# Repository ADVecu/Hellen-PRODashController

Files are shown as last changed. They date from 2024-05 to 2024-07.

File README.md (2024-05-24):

# FAQ

Q: How do I get latest hellen-one?

A: ``.github/workflows/update-hellen-one-reference.yaml`` is set to pull latest hellen daily!

Q: I get "Cannot parse position" with negative value?

A: Please move origin point into left-bottom corner of the board since we cannot parse negative coordinates at the moment. See https://github.com/andreika-git/hellen-one/issues/349

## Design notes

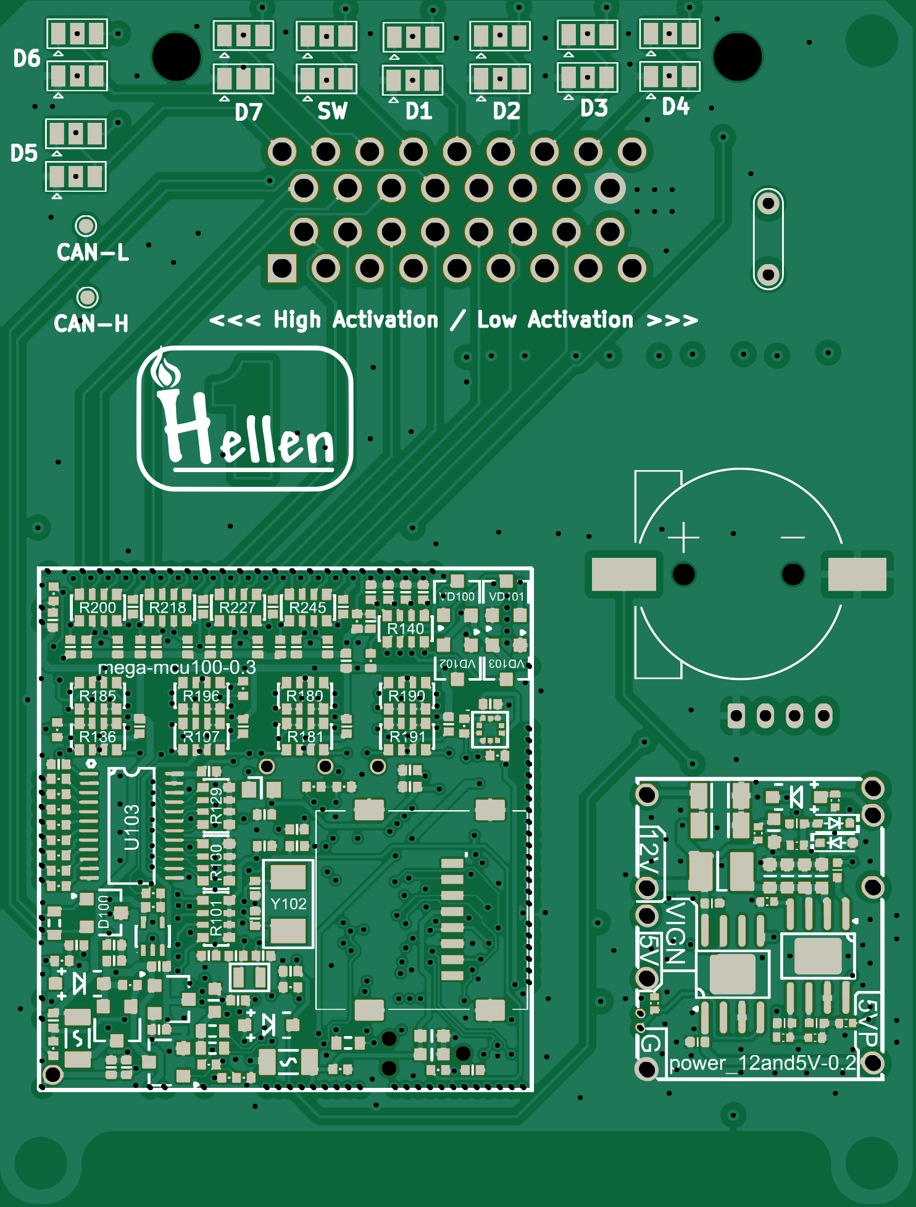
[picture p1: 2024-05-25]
boards/PRODashController-A/board/misc/PRODashController-A-bottom.png

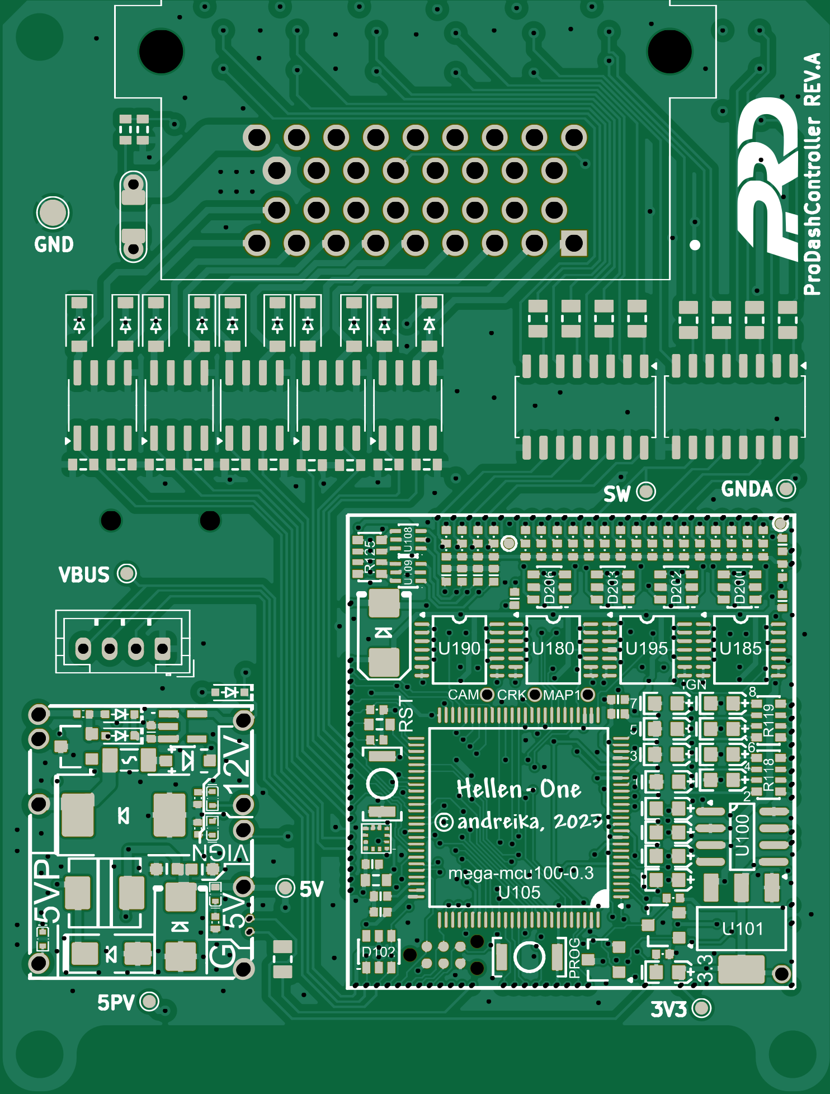
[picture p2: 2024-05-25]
boards/PRODashController-A/board/misc/PRODashController-A-top.png

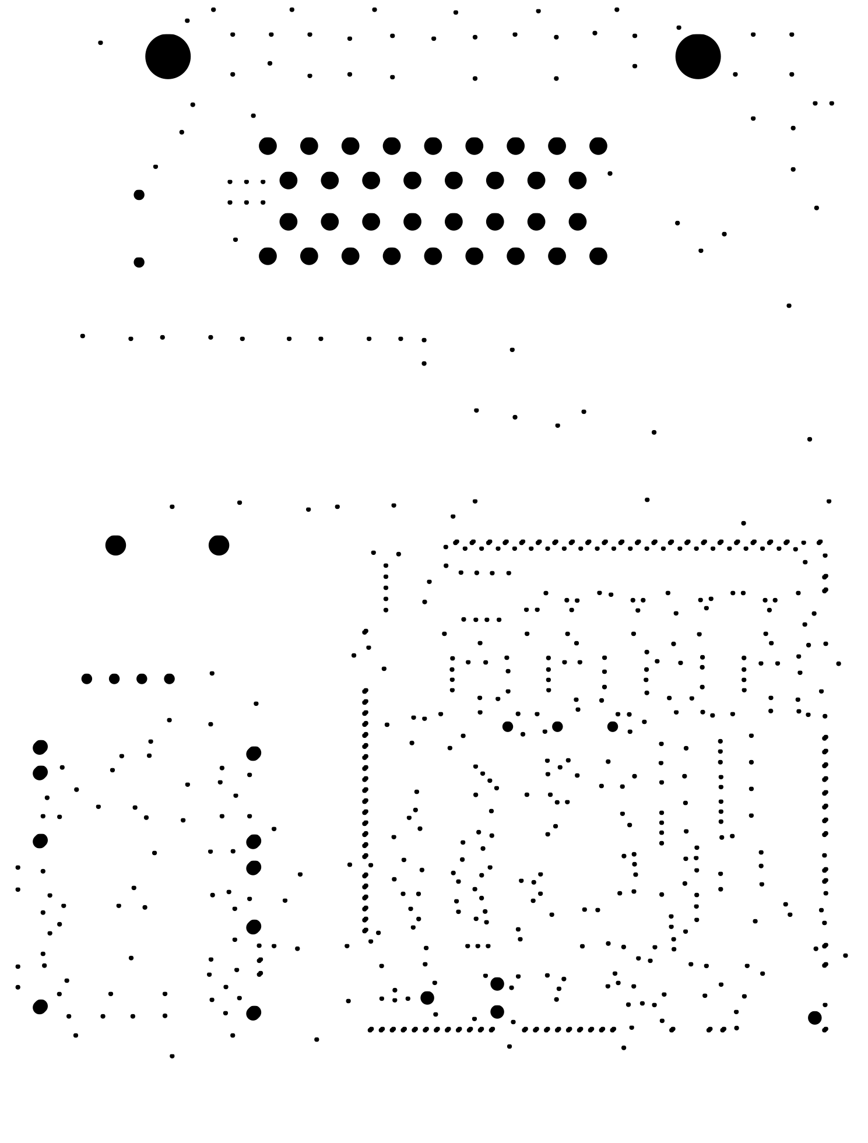
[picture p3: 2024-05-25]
boards/PRODashController-A/board/misc/PRODashController-A-outline.png

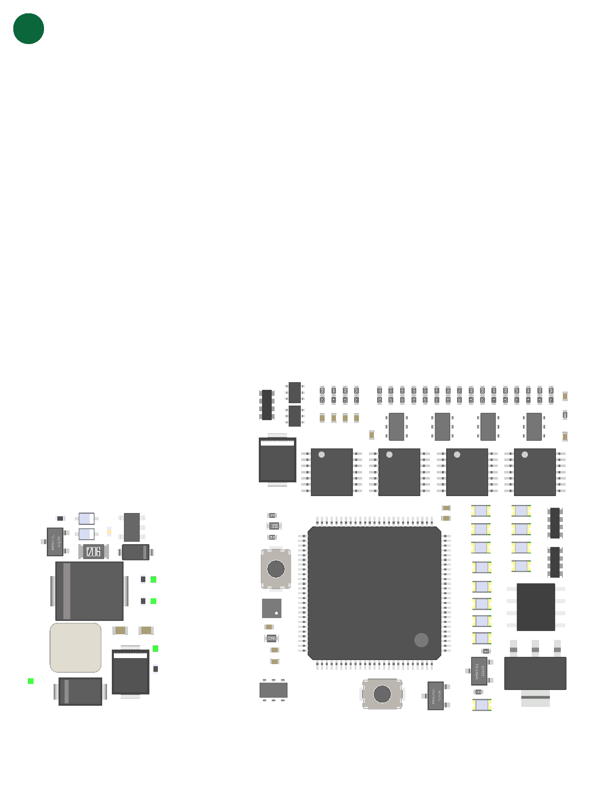
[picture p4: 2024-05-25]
boards/PRODashController-A/board/PRODashController-A.png

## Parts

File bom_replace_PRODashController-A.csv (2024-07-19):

#remove +5V pull-ups from SPI1 because we use it with +3.3v accelerometer
R103,
R105,
#remove jumper resistor connecting BOOT1 with A22 input line because we use STM32F4
R131,
#PWR_EN not used as GPIO
R142,
# DC-DC Inductor
L421,"MWSA0503S-100MT","MWSA0503","C408412"
L420,"NLCV32T-2R2M-EF","L1210","C250227"
#Fuses
F410,"nSMD050-24V","SMD1206","C70076"
# TLS115
U411,"TLS115B0EJXUMA1","PG-DSO-8","C3747428"
#Cost
U106,
#20MHz crystal
Y102,"TXM20M0002503LFBEO00T","SMD5032-2P","C362485"
#SD Card
J100,"TF-014-H16","SMD","C125814"
# cost
D411,"PSM712-LF","SOT-23","C5180294"
#LEDs
D109,
D110,
D111,
D112,
D113,
D114,
D115,
D116,
"D104,D108","GREEN_LED","LED0603","C965804"
D105,"BLUE_LED","LED0603","C497940"
"LED1, LED2, LED3, LED4","BLUE_LED","LED0402","C2844007"
#IGN not used
U103,
R110,
R111,
R112,
R113,
R114,
R115,
R116,
R117,
R118,
R119,
#Accelerometer
U107,
#CRANK BUTTON1: UP 680k 1n
R222,"680k","R0402","C163456"
R226,
C211,"1n","C0402","C1523"
#CAM BUTTON2: UP 680k 1n
R220,"680k","R0402","C163456"
R224,
C209,"1n","C0402","C1523"
#VSS FLEX: UP 10k 1n
R219,"10k","R0402","C25744"
R223,
C208,"1n","C0402","C1523"
#TPS IN_VMAIN: DOWN 680k 10n
R204,
R208,
C203,"100n","C0402","C307331"
#PPS PPS1: DOWN 680k 10n
R203,
R207,"680k","R0402","C163456"
C202,"10n","C0402","C15195"
#IAT IAT: UP 4.7k 10n
R202,"4.7k","R0402","C25900"
R206,
C201,"10n","C0402","C15195"
#CLT CLT: UP 4.7k 10n
R201,"4.7k","R0402","C25900"
R205,
C200,"10n","C0402","C15195"
#O2S SW_ON: UP 680k 10n
R230,"680k","R0402","C163456"
R234,
C214,"10n","C0402","C15195"
#O2S2 AUX2: DOWN 680k 10n
R231,
R235,"680k","R0402","C163456"
C215,"10n","C0402","C15195"
#MAP1 MAP: DOWN 680k 1n
R228,
R232,"680k","R0402","C163456"
C212,"1n","C0402","C1523"
#MAP2 INTERNAL_MAP: DOWN 680k 1n
R229,
R233,"680k","R0402","C163456"
C213,"1n","C0402","C1523"
#AUX1 TPS2: DOWN 680k 10n
R246,
R250,"680k","R0402","C163456"
C225,"10n","C0402","C15195"
#AUX2 PPS2: DOWN 680k 10n
R247,
R251,"680k","R0402","C163456"
C226,"10n","C0402","C15195"
#AUX3 AUX3: DOWN 680k 10n
R248,
R252,"680k","R0402","C163456"
C227,"10n","C0402","C15195"
#AUX4 VMAIN: DOWN 680K 100n
R249,
R253,"680k","R0402","C163456"
C228,"100n","C0402","C307331"
#KNOCK KNOCK: UP 680k 1n
R221,"680k","R0402","C163456"
R225,
C210,"1n","C0402","C1523"
#D1 HALL1: UP 4.7k 1n
R124,"4.7k","R0402","C25900"
R136,
C143,"1n","C0402","C1523"
#D2 HALL2: UP 4.7k 1n
R126,"4.7k","R0402","C25900"
R137,
C144,"1n","C0402","C1523"
#D3 HALL3: UP 4.7k 1n
R132,"4.7k","R0402","C25900"
R138,
C145,"1n","C0402","C1523"
#D4 BUTTON3: UP 680k 1n
R135,"680k","R0402","C163456"
R139,
C146,"1n","C0402","C1523"

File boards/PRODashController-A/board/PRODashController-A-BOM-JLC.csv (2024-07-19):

Comment | Designator | Footprint | LCSC Part #
CR1220 | BT1 | CR1220-2 | C70381
B5819W | D1, D2, D3, D4, D5, D6, D7, D8, D9, D10, D101, D107, D416, D417 | SOD-123 | C8598
1N4148WS | D11, D410, D412, D413, D414 | SOD-323 | C2128
12H1500D | F1 | PAD-1206-PAD | C182446
USB | J2 | JST_PH_B4B-PH-K_1x04_P2.00mm_Vertical | C5305780
4.7k | R1, R2, R3, R4, R5, R6, R7, R8, R9, R10 | R0603 | C23162
33k | R11, R120 | R0603 | C4216
6.8k | R12 | R0603 | C23212
0 | R13 | R0805 | C17477
2k7 | R14, R15, R16, R17, R18, R19, R20, R21 | R0805 | C17530
VNLD5160TR-E | U1, U2, U3, U4, U5 | SO8 | C377942
LTV-247 | U6, U7 | SOP-16_4.4x10.4mm_P1.27mm | C115451
TJA1051T/3/1J | U100 | SO8 | C38695
STM32F429VGT6 | U105 | LQFP100 | C95448
SRV05-4-P-T7 | D102, D200, D202, D203, D206 | SOT23-6 | C85364
SN74LVC1G06DCKR | U110 | SOT-353 | C7828
SMD1206B035TF/16 | F100, F101 | R1206 | C269114
REF3033 | U102 | SOT-23 | C36658
PESD1CAN | D100 | SOT-23 | C343993
P6SMB6.8CA | D205, D421 | SMB | C78395
MCP6004 | U180, U185, U190, U195 | TSSOP14 | C50282
LED-YELLOW-0603 | D106 | LED-0603 | C72038
LED-RED-0603 | D103 | LED-0603 | C2286
LDL1117S33R | U101 | SOT-223 | C435835
BTN | S100, S101 | SMD-2_2.9x3.9x1.7 | C115357
BLM18AG601SN1D | L100 | L0603 | C19330
BAT54S | VD100, VD101, VD102, VD103 | SOT-23 | C47546
AO3401A | Q100, Q102 | SOT-23 | C15127
AO3400A | Q101, Q103 | SOT-23 | C20917
680k | R222, R220, R207, R230, R235, R232, R233, R250, R251, R252, R253, R221, R135 | R0402 | C163456
510 | R133, R134 | R0603 | C23193
510 | R254, R255, R256, R258 | R0402 | C25123
470 | R101 | R0603-4 | C25510
120 | R100 | R0603 | C22787
100n | C100, C101, C105, C108, C111, C112, C113, C119, C120, C122, C124, C126, C127, C130, C134, C147, C180, C185, C190, C195, C220, C221, C222 | C0402 | C1525
100 | R104, R106 | R0603 | C22775
74LVC2G17GW,125 | U108, U109 | SOT-363 | C80500
32.768 kHz | Y101 | SMD2012 | C99009
10u | C117, C421, C422, C423, C424, C425, C426 | C0603 | C96446
18p | C132, C136 | C0402 | C1549
12p | C115, C116 | C0402 | C1547
10n | C428, C202, C201, C200, C214, C215, C225, C226, C227 | C0402 | C15195
10k | R102, R107, R108, R109, R121, R127, R128, R141, R421, R426, R427, R219 | R0402 | C25744
10k | R129, R130, R140 | R0603-4 | C29718
5.1k | R195 | R0402 | C25905
4.7u | C102, C103, C104, C106, C107, C137, C138, C140 | C0402 | C23733
4.7k | R125, R180, R181, R185, R186, R190, R191, R196, R197, R200, R218, R227, R245 | R0603-4 | C66697
4.7k | R144, R428, R202, R201, R124, R126, R132 | R0402 | C25900
2.2u | C114, C131, C223, C224, C229 | C0402 | C12530
2.2k | R122, R123, R146, R147 | R0402 | C25879
1u | C133 | C0603 | C519560
1n | C135, C139, C141, C142, C211, C209, C208, C212, C213, C210, C143, C144, C145, C146 | C0402 | C1523
0 | R143, R145, R148 | R0402 | C17168
47u | C410, C412 | C1206 | C96123
100n | C411, C413, C420, C203, C228 | C0402 | C307331
1u | C414, C415 | C0402 | C52923
4.7u | C427 | C0603 | C19666
220p | C429 | C0402 | C1530
SMCJ30A | D418 | SMC | C310046
SS34 | D420 | SMA | C8678
6.8k | R410, R413 | R0402 | C25917
33k | R411, R424, R425 | R0402 | C25779
1 | R420 | R0402 | C25086
68k | R422 | R0402 | C36871
12k | R423 | R0402 | C25752
MIC5205-3.3YM5 | U410 | SOT23-5 | C37970
LMR14020 | U420 | SOP8 | C187824
MWSA0503S-100MT | L421 | MWSA0503 | C408412
NLCV32T-2R2M-EF | L420 | L1210 | C250227
nSMD050-24V | F410 | SMD1206 | C70076
TLS115B0EJXUMA1 | U411 | PG-DSO-8 | C3747428
TXM20M0002503LFBEO00T | Y102 | SMD5032-2P | C362485
TF-014-H16 | J100 | SMD | C125814
PSM712-LF | D411 | SOT-23 | C5180294
GREEN_LED | D104, D108 | LED0603 | C965804
BLUE_LED | D105 | LED0603 | C497940
BLUE_LED | LED1, LED2, LED3, LED4 | LED0402 | C2844007

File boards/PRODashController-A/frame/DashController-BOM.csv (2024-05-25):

Comment | Designator | Footprint | LCSC Part #
CR1220 | BT1 | CR1220-2 | C70381
B5819W | D1 | SOD-123 | C8598
B5819W | D2 | SOD-123 | C8598
B5819W | D3 | SOD-123 | C8598
B5819W | D4 | SOD-123 | C8598
B5819W | D5 | SOD-123 | C8598
B5819W | D6 | SOD-123 | C8598
B5819W | D7 | SOD-123 | C8598
B5819W | D8 | SOD-123 | C8598
B5819W | D9 | SOD-123 | C8598
B5819W | D10 | SOD-123 | C8598
1N4148WS | D11 | SOD-323 | C2128
12H1500D | F1 | PAD-1206-PAD | C182446
LOGO | G1 | LOGO
LOGO | G2 | PRO_LOGO
6437288-1 | J1 | TE_6437288-1
USB | J2 | JST_PH_B4B-PH-K_1x04_P2.00mm_Vertical | C5305780
Module:mega-mcu100/0.3 | M1 | mega-mcu100
Module:power_12and5V/0.2 | M2 | power_12and5V
4.7k | R1 | R0603 | C23162
4.7k | R2 | R0603 | C23162
4.7k | R3 | R0603 | C23162
4.7k | R4 | R0603 | C23162
4.7k | R5 | R0603 | C23162
4.7k | R6 | R0603 | C23162
4.7k | R7 | R0603 | C23162
4.7k | R8 | R0603 | C23162
4.7k | R9 | R0603 | C23162
4.7k | R10 | R0603 | C23162
33k | R11 | R0603 | C4216
6.8k | R12 | R0603 | C23212
0 | R13 | R0805 | C17477
2k7 | R14 | R0805 | C17530
2k7 | R15 | R0805 | C17530
2k7 | R16 | R0805 | C17530
2k7 | R17 | R0805 | C17530
2k7 | R18 | R0805 | C17530
2k7 | R19 | R0805 | C17530
2k7 | R20 | R0805 | C17530
2k7 | R21 | R0805 | C17530
VBUS | TP1 | TestPoint_Pad_D1.0mm
+5V | TP2 | TestPoint_Pad_D1.0mm
GND | TP3 | TestPoint_Pad_D2.0mm
+5VP | TP4 | TestPoint_Pad_D1.0mm
GNDA | TP5 | TestPoint_Pad_D1.0mm
+3.3V | TP7 | TestPoint_Pad_D1.0mm
CANH | TP9 | TestPoint_Pad_D1.0mm
CANL | TP10 | TestPoint_Pad_D1.0mm
SWON | TP11 | TestPoint_Pad_D1.0mm
VNLD5160TR-E | U1 | SO8 | C377942
VNLD5160TR-E | U2 | SO8 | C377942
VNLD5160TR-E | U3 | SO8 | C377942
VNLD5160TR-E | U4 | SO8 | C377942
VNLD5160TR-E | U5 | SO8 | C377942
LTV-247 | U6 | SOP-16_4.4x10.4mm_P1.27mm | C115451
LTV-247 | U7 | SOP-16_4.4x10.4mm_P1.27mm | C115451

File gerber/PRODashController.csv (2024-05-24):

Comment | Designator | Footprint | LCSC Part #
CR1220 | BT1 | Hellen:CR1220-2 | C70381
B5819W | D1 | Hellen:SOD-123 | C8598
B5819W | D2 | Hellen:SOD-123 | C8598
B5819W | D3 | Hellen:SOD-123 | C8598
B5819W | D4 | Hellen:SOD-123 | C8598
B5819W | D5 | Hellen:SOD-123 | C8598
B5819W | D6 | Hellen:SOD-123 | C8598
B5819W | D7 | Hellen:SOD-123 | C8598
B5819W | D8 | Hellen:SOD-123 | C8598
B5819W | D9 | Hellen:SOD-123 | C8598
B5819W | D10 | Hellen:SOD-123 | C8598
1N4148WS | D11 | Hellen:SOD-323 | C2128
12H1500D | F1 | Hellen:PAD-1206-PAD | C182446
LOGO | G1 | Hellen:LOGO
LOGO | G2 | PRO_LOGO:PRO_LOGO
6437288-1 | J1 | 6437288-1:TE_6437288-1
USB | J2 | Connector_JST:JST_PH_B4B-PH-K_1x04_P2.00mm_Vertical | C5305780
Module:mega-mcu100/0.3 | M1 | Hellen:mega-mcu100
Module-power_12and5V-0.2 | M2 | Hellen:power_12and5V
4.7k | R1 | Hellen:R0603 | C23162
4.7k | R2 | Hellen:R0603 | C23162
4.7k | R3 | Hellen:R0603 | C23162
4.7k | R4 | Hellen:R0603 | C23162
4.7k | R5 | Hellen:R0603 | C23162
4.7k | R6 | Hellen:R0603 | C23162
4.7k | R7 | Hellen:R0603 | C23162
4.7k | R8 | Hellen:R0603 | C23162
4.7k | R9 | Hellen:R0603 | C23162
4.7k | R10 | Hellen:R0603 | C23162
33k | R11 | Hellen:R0603 | C4216
6.8k | R12 | Hellen:R0603 | C23212
0 | R13 | Hellen:R0805 | C17477
2k7 | R14 | Hellen:R0805 | C17530
2k7 | R15 | Hellen:R0805 | C17530
2k7 | R16 | Hellen:R0805 | C17530
2k7 | R17 | Hellen:R0805 | C17530
2k7 | R18 | Hellen:R0805 | C17530
2k7 | R19 | Hellen:R0805 | C17530
2k7 | R20 | Hellen:R0805 | C17530
2k7 | R21 | Hellen:R0805 | C17530
VBUS | TP1 | TestPoint:TestPoint_Pad_D1.0mm
+5V | TP2 | TestPoint:TestPoint_Pad_D1.0mm
GND | TP3 | TestPoint:TestPoint_Pad_D2.0mm
+5VP | TP4 | TestPoint:TestPoint_Pad_D1.0mm
GNDA | TP5 | TestPoint:TestPoint_Pad_D1.0mm
+3.3V | TP7 | TestPoint:TestPoint_Pad_D1.0mm
CANH | TP9 | TestPoint:TestPoint_Pad_D1.0mm
CANL | TP10 | TestPoint:TestPoint_Pad_D1.0mm
SWON | TP11 | TestPoint:TestPoint_Pad_D1.0mm
VNLD5160TR-E | U1 | Package_SO:SOIC-8_3.9x4.9mm_P1.27mm | C377942
VNLD5160TR-E | U2 | Package_SO:SOIC-8_3.9x4.9mm_P1.27mm | C377942
VNLD5160TR-E | U3 | Package_SO:SOIC-8_3.9x4.9mm_P1.27mm | C377942
VNLD5160TR-E | U4 | Package_SO:SOIC-8_3.9x4.9mm_P1.27mm | C377942
VNLD5160TR-E | U5 | Package_SO:SOIC-8_3.9x4.9mm_P1.27mm | C377942
LTV-247 | U6 | Package_SO:SOP-16_4.4x10.4mm_P1.27mm | C115451
LTV-247 | U7 | Package_SO:SOP-16_4.4x10.4mm_P1.27mm | C115451

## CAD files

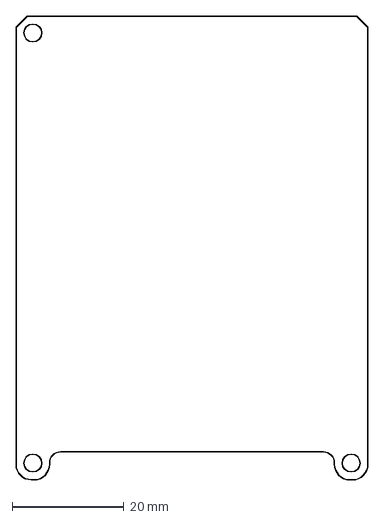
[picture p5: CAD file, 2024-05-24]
PCBoutline.dxf
63.0 x 83.0 mm

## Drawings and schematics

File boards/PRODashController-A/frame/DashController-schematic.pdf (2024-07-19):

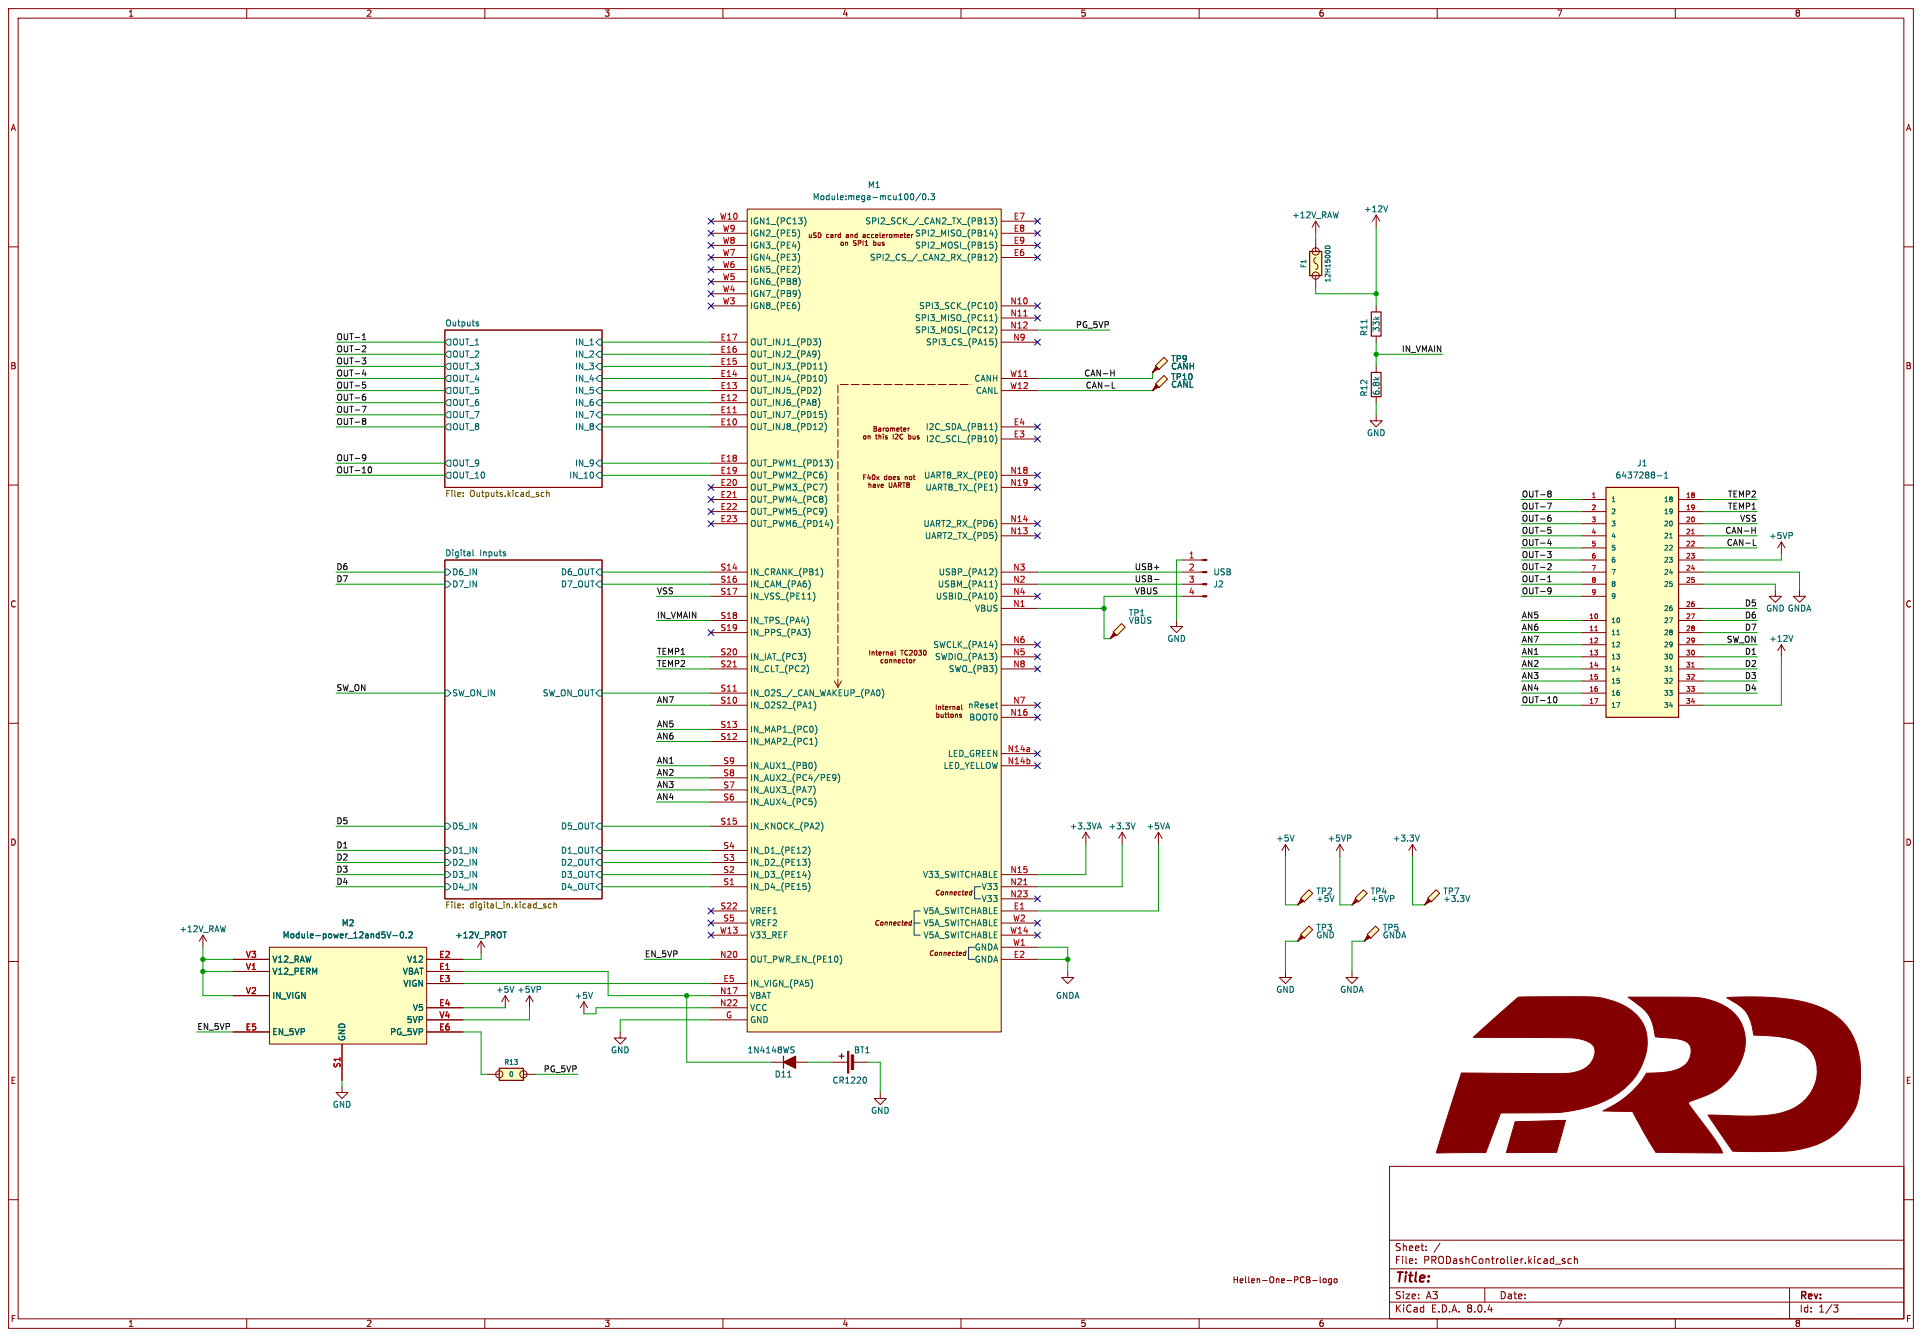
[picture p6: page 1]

Hellen-One-PCB-logo R13

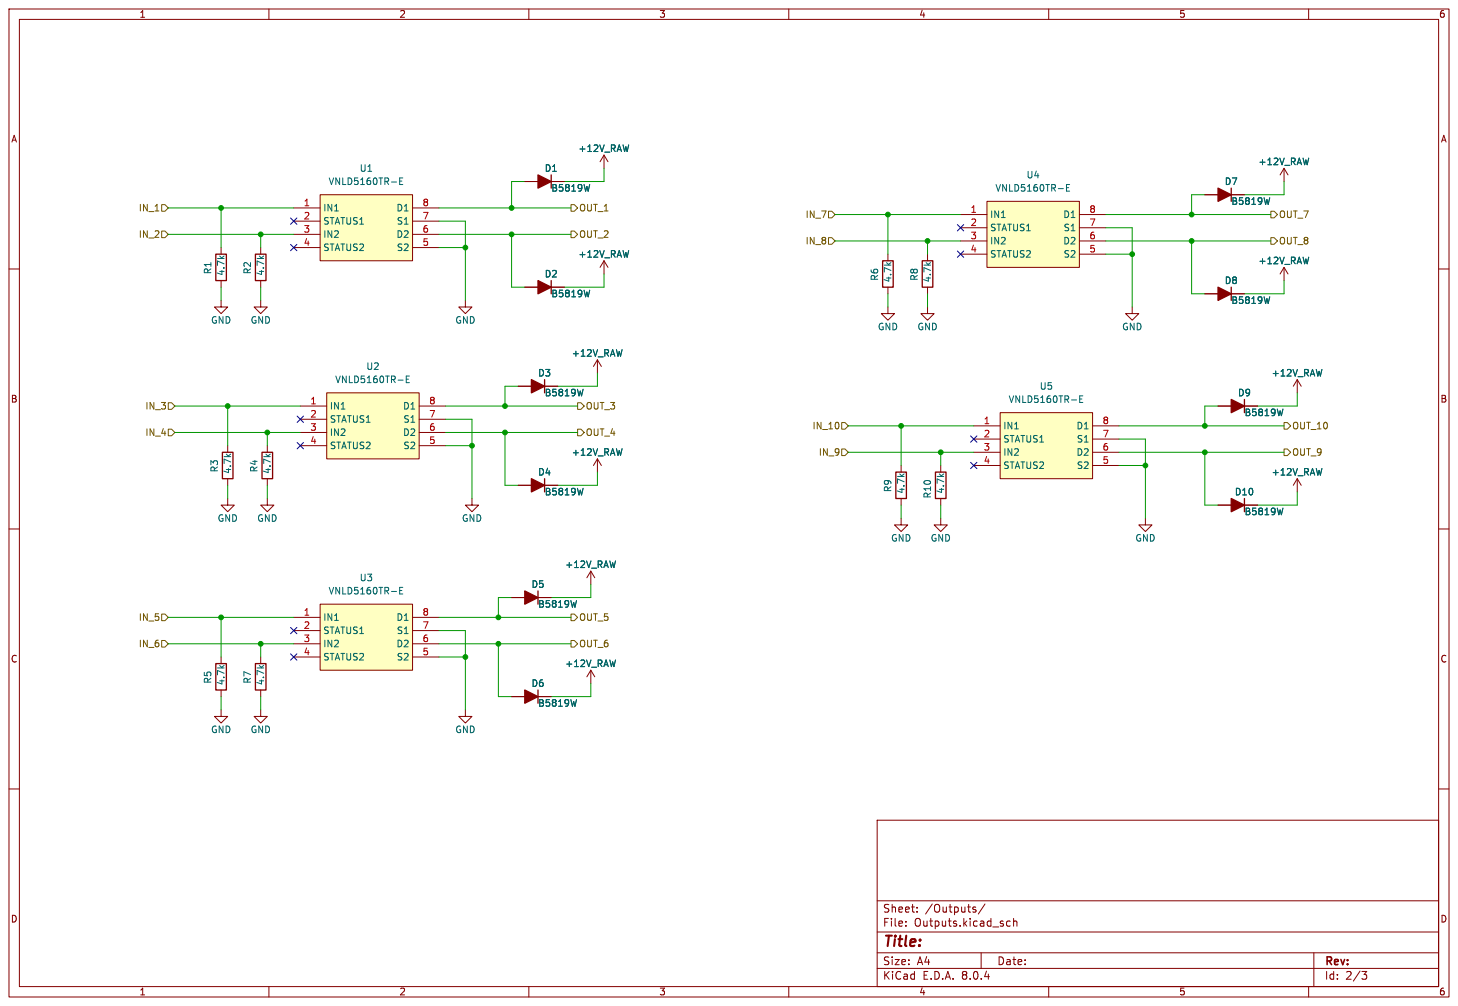
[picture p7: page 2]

Id: 2/3 Title: File: Outputs.kicad_sch Sheet: /Outputs/

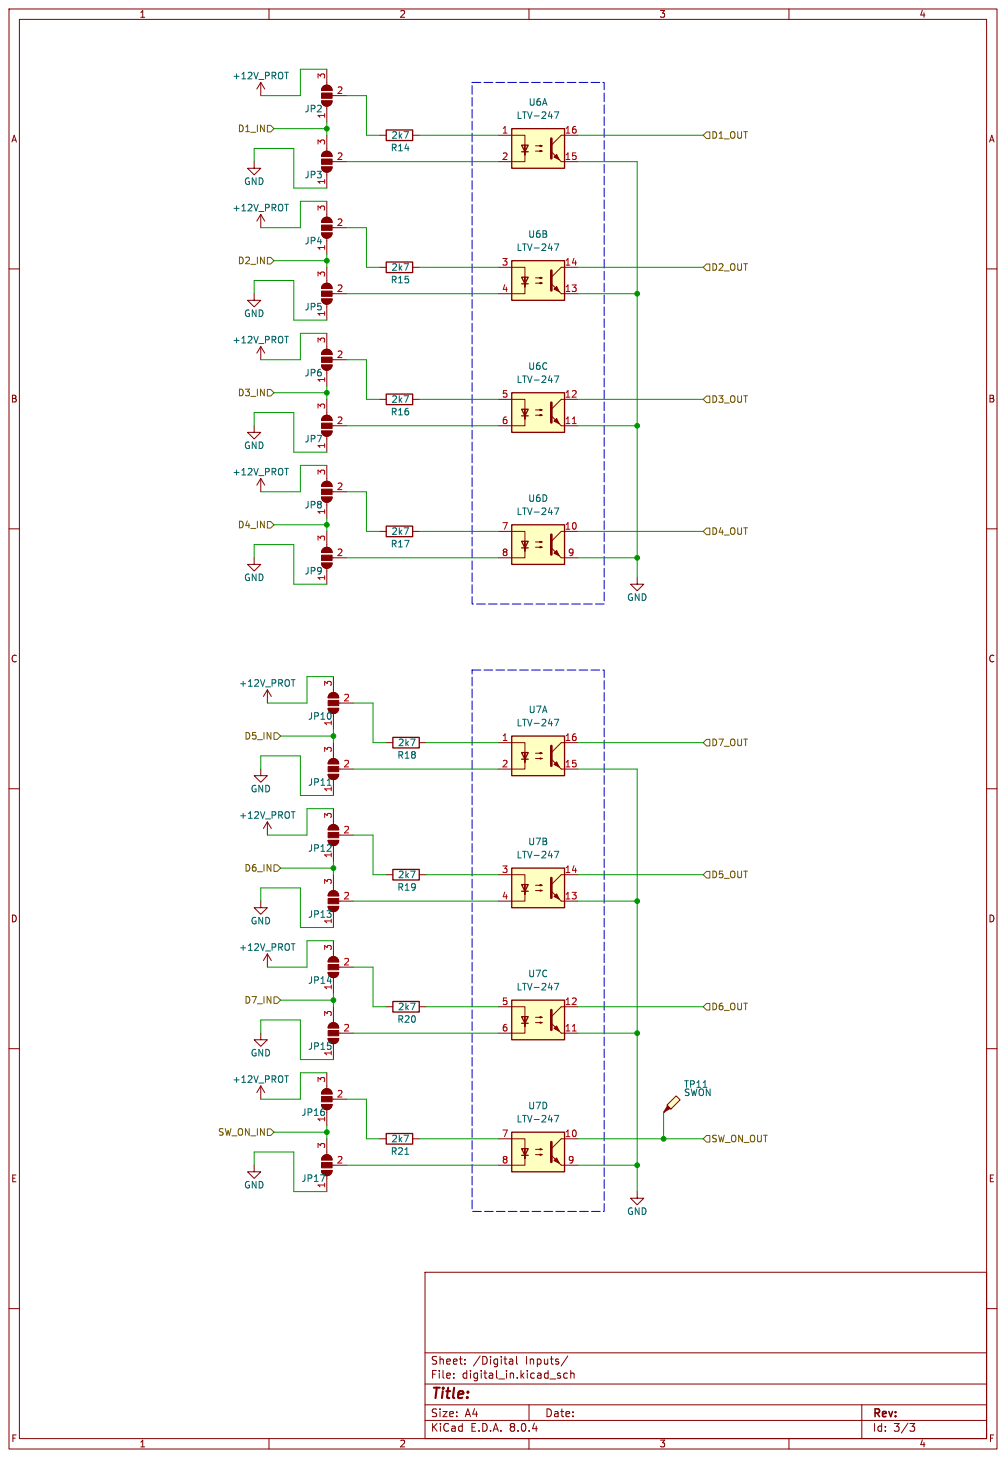
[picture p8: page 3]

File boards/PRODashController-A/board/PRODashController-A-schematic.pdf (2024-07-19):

VBUS | N1 SPI3_SCK_(PC10) | N10 SPI3_MISO_(PC11) | N11 SPI3_MOSI_(PC12) | N12 UART2_TX_(PD5) | N13 UART2_RX_(PD6) | N14
IGN1_(PC13) W10 | CANH | W11 CANL | W12 V33_REF W13 | V5A_SWITCHABLE W14 V5A_SWITCHABLE | W2


Hellen-One-PCB-logo R13

IN2 3 | STATUS2 4 | S2 | 5 D2 | 6 S1 | 7 D1 | 8 U1 VNLD5160TR-E | D6B5819W

D Date: KiCad; E.D.A. 8.0.4 Size: A4; Rev:; GNDGND; STATUS1 2; STATUS2 4; 8 U4 VNLD5160TR-E; 8 U3 VNLD5160TR-E; GND; R⁸ 4.7k GND GNDGND; 8 U2 VNLD5160TR-E; R⁹ 4.7k GND R¹⁰ 4.7k GND R¹ 4.7k; +12V_RAW; 8 U5 VNLD5160TR-E; GND R³ 4.7k; GND R⁵ 4.7k; R⁷ 4.7k GND; OUT_7; OUT_10; OUT_8 OUT_3 OUT_4; OUT_9 OUT_6 OUT_2; OUT_5; OUT_1 D4B5819W

Id: 2/3 Title: File: Outputs.kicad_sch Sheet: /Outputs/

JP5 GND | 1 | 2 ³
JP2 1 | 2 ³


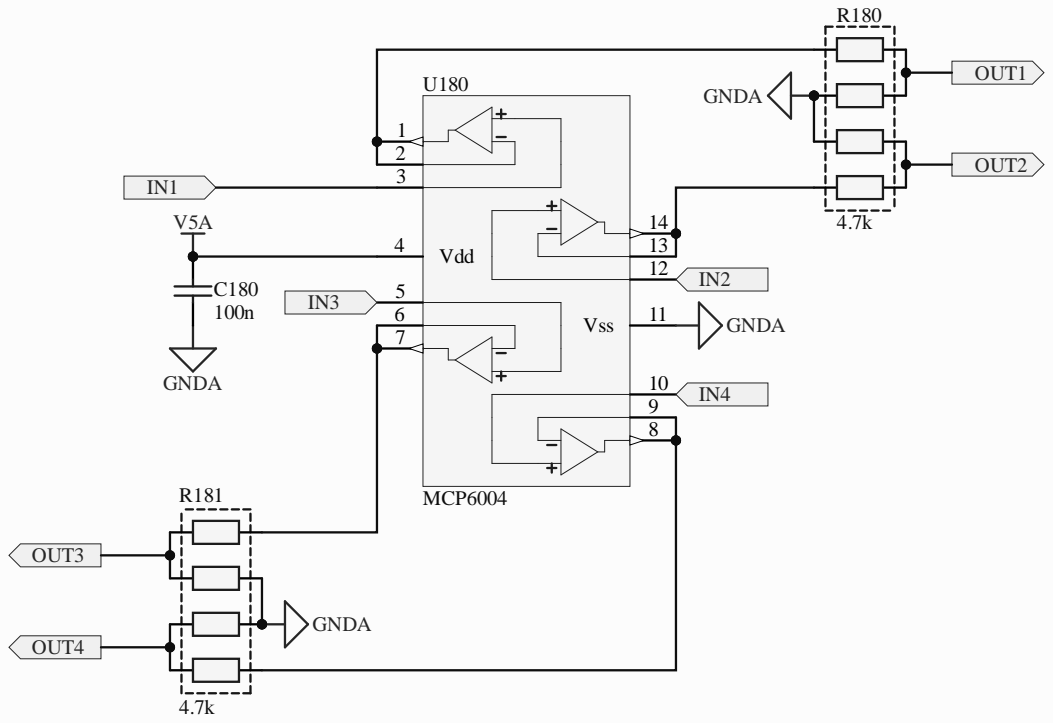
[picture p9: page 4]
Vdd 4; Vss 6; MCP6004; GNDA; OUT1; OUT2; OUT3; OUT4; C180 PIC18001 100n; PIC18002 COC3; PIR18001; PIR18002; PIR18003; PIR18004; PIR18005; PIR18006; PIR18007; PIR18008; COR5; PIR18101; PIR18102; PIR18103; PIR18105; PIR18104; PIR18106; PIR18107; PIR18108; COR6; PIU18001; PIU18002; PIU18003; PIU18004; PIU18005; PIU18006; PIU18007; PIU18008; PIU18009; PIU180010; PIU180011; PIU180012; PIU180013; PIU180014; COU2; PIC18001; POOUT2; POOUT1; POOUT3; POOUT4; POIN1; POIN3 PIU18005; PIU180010 POIN4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

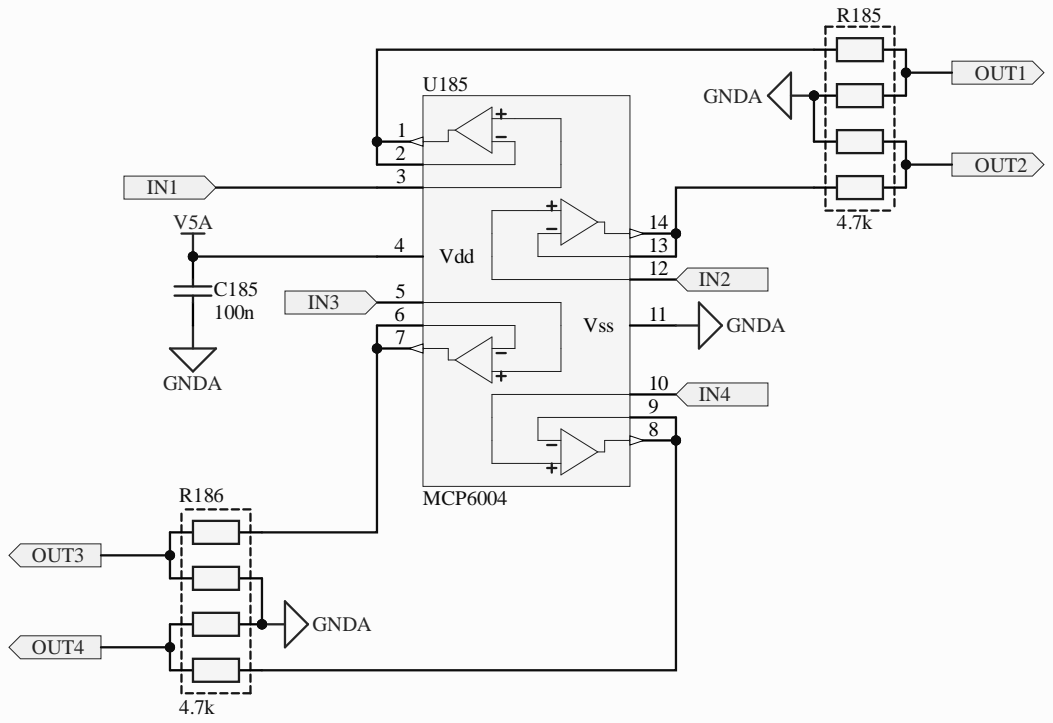
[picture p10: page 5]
Vdd 4; Vss 6; MCP6004; GNDA; OUT1; OUT2; OUT3; OUT4; C185 PIC18501 100n; PIC18502 COC3; PIR18501; PIR18502; PIR18503; PIR18504; PIR18505; PIR18506; PIR18507; PIR18508; COR5; PIR18601; PIR18602; PIR18603; PIR18605; PIR18604; PIR18606; PIR18607; PIR18608; COR6; PIU18501; PIU18502; PIU18503; PIU18504; PIU18505; PIU18506; PIU18507; PIU18508; PIU18509; PIU185010; PIU185011; PIU185012; PIU185013; PIU185014; COU2; PIC18501; POOUT2; POOUT1; POOUT3; POOUT4; POIN1; POIN3 PIU18505; PIU185010 POIN4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

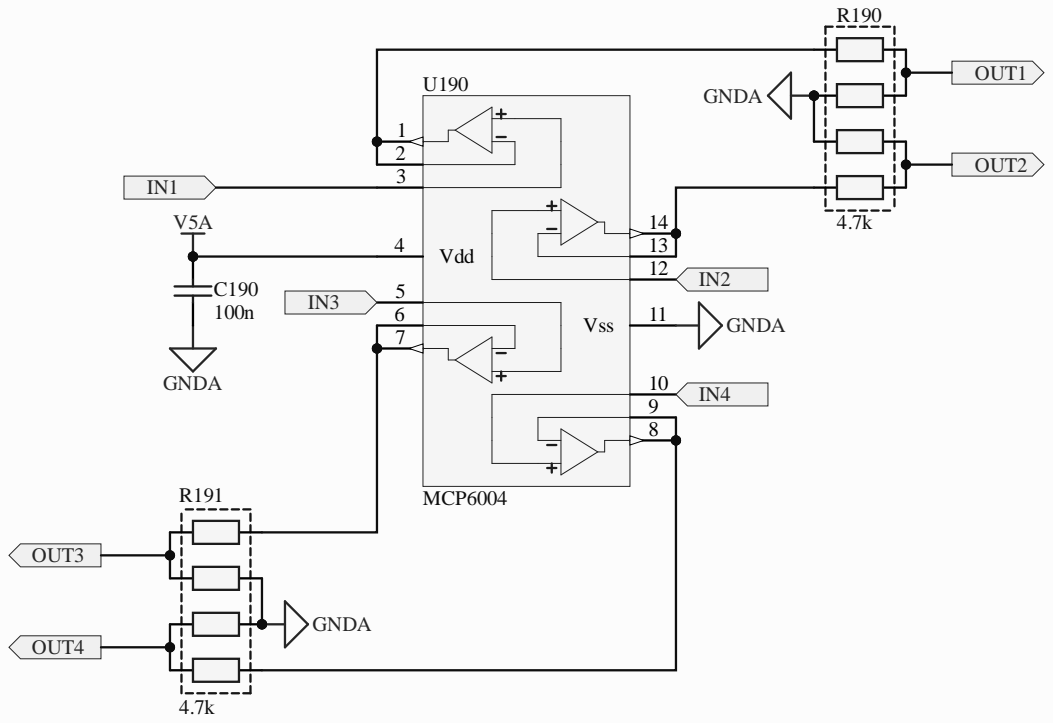
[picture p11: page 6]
Vdd 4; Vss 6; MCP6004; GNDA; OUT1; OUT2; OUT3; OUT4; C190 PIC19001 100n; PIC19002 COC3; PIR19001; PIR19002; PIR19003; PIR19004; PIR19005; PIR19006; PIR19007; PIR19008; COR5; PIR19101; PIR19102; PIR19103; PIR19105; PIR19104; PIR19106; PIR19107; PIR19108; COR6; PIU19001; PIU19002; PIU19003; PIU19004; PIU19005; PIU19006; PIU19007; PIU19008; PIU19009; PIU190010; PIU190011; PIU190012; PIU190013; PIU190014; COU2; PIC19001; POOUT2; POOUT1; POOUT3; POOUT4; POIN1; POIN3 PIU19005; PIU190010 POIN4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

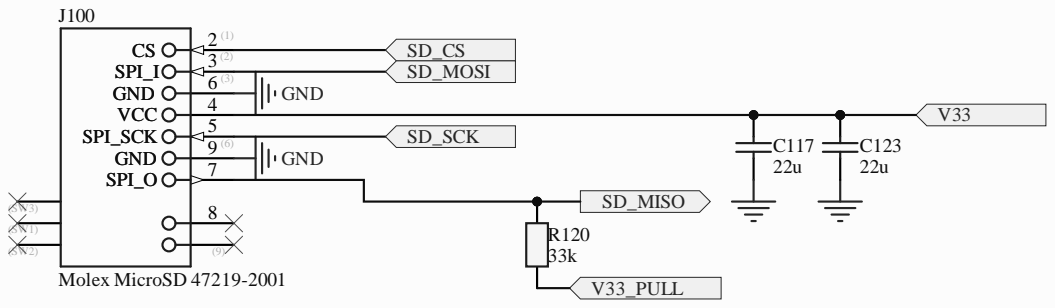
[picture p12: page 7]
SPI_; VCC; 5 SPI_SCK; 7 SPI_O; lex MicroSD; _MIS

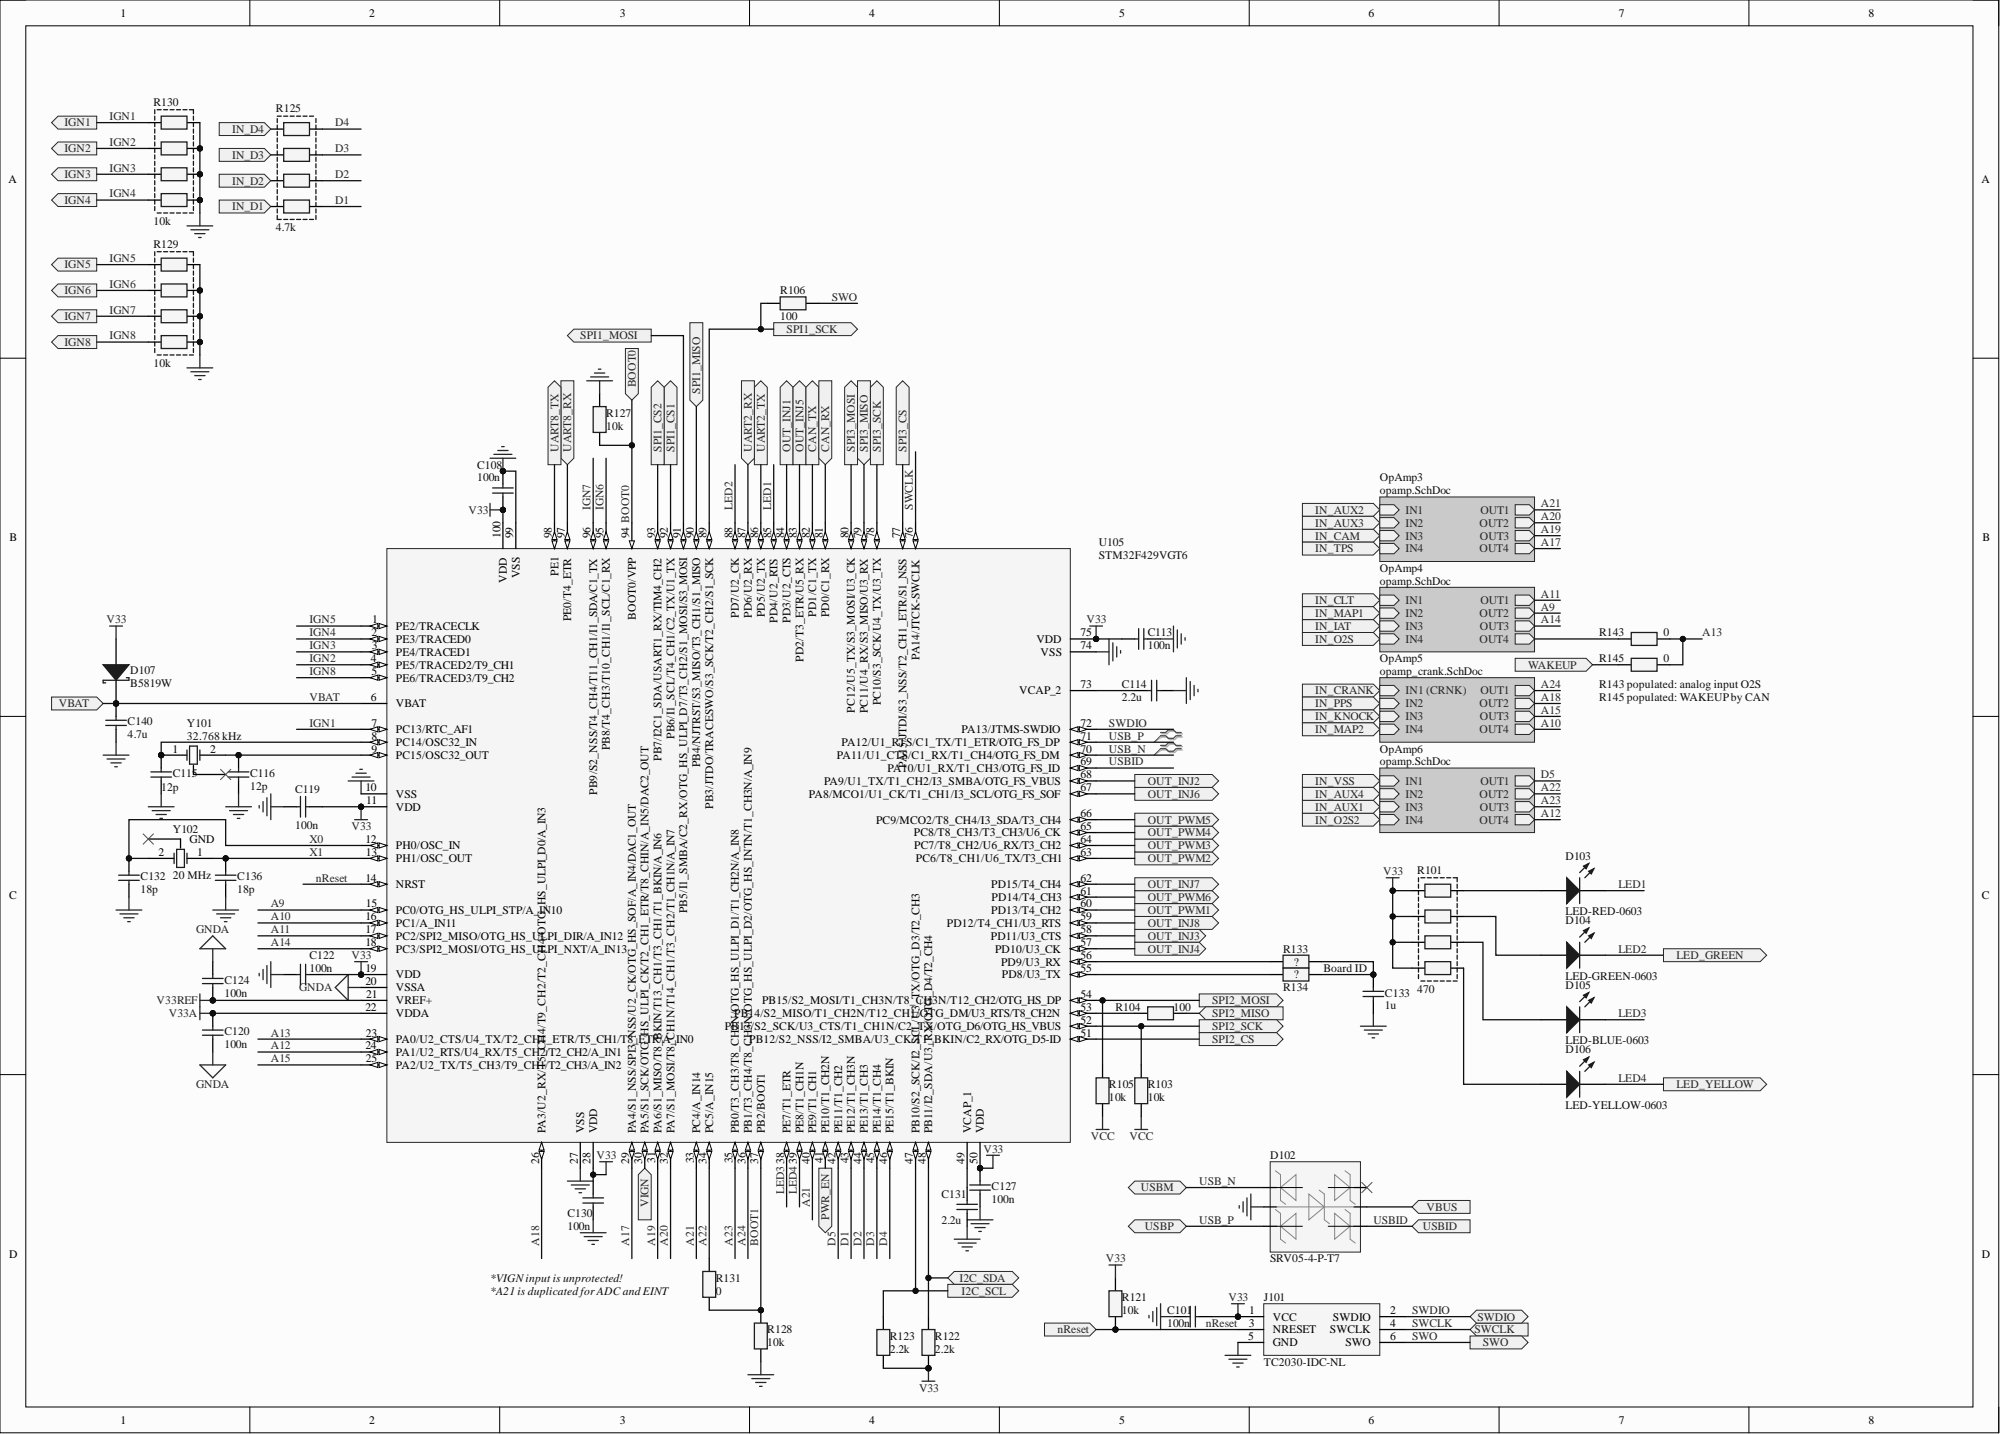
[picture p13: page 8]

R143 populated: analog input O2S
R145 populated: WAKEUP by CAN

*VIGN input is unprotected!
*A21 is duplicated for ADC and EINT

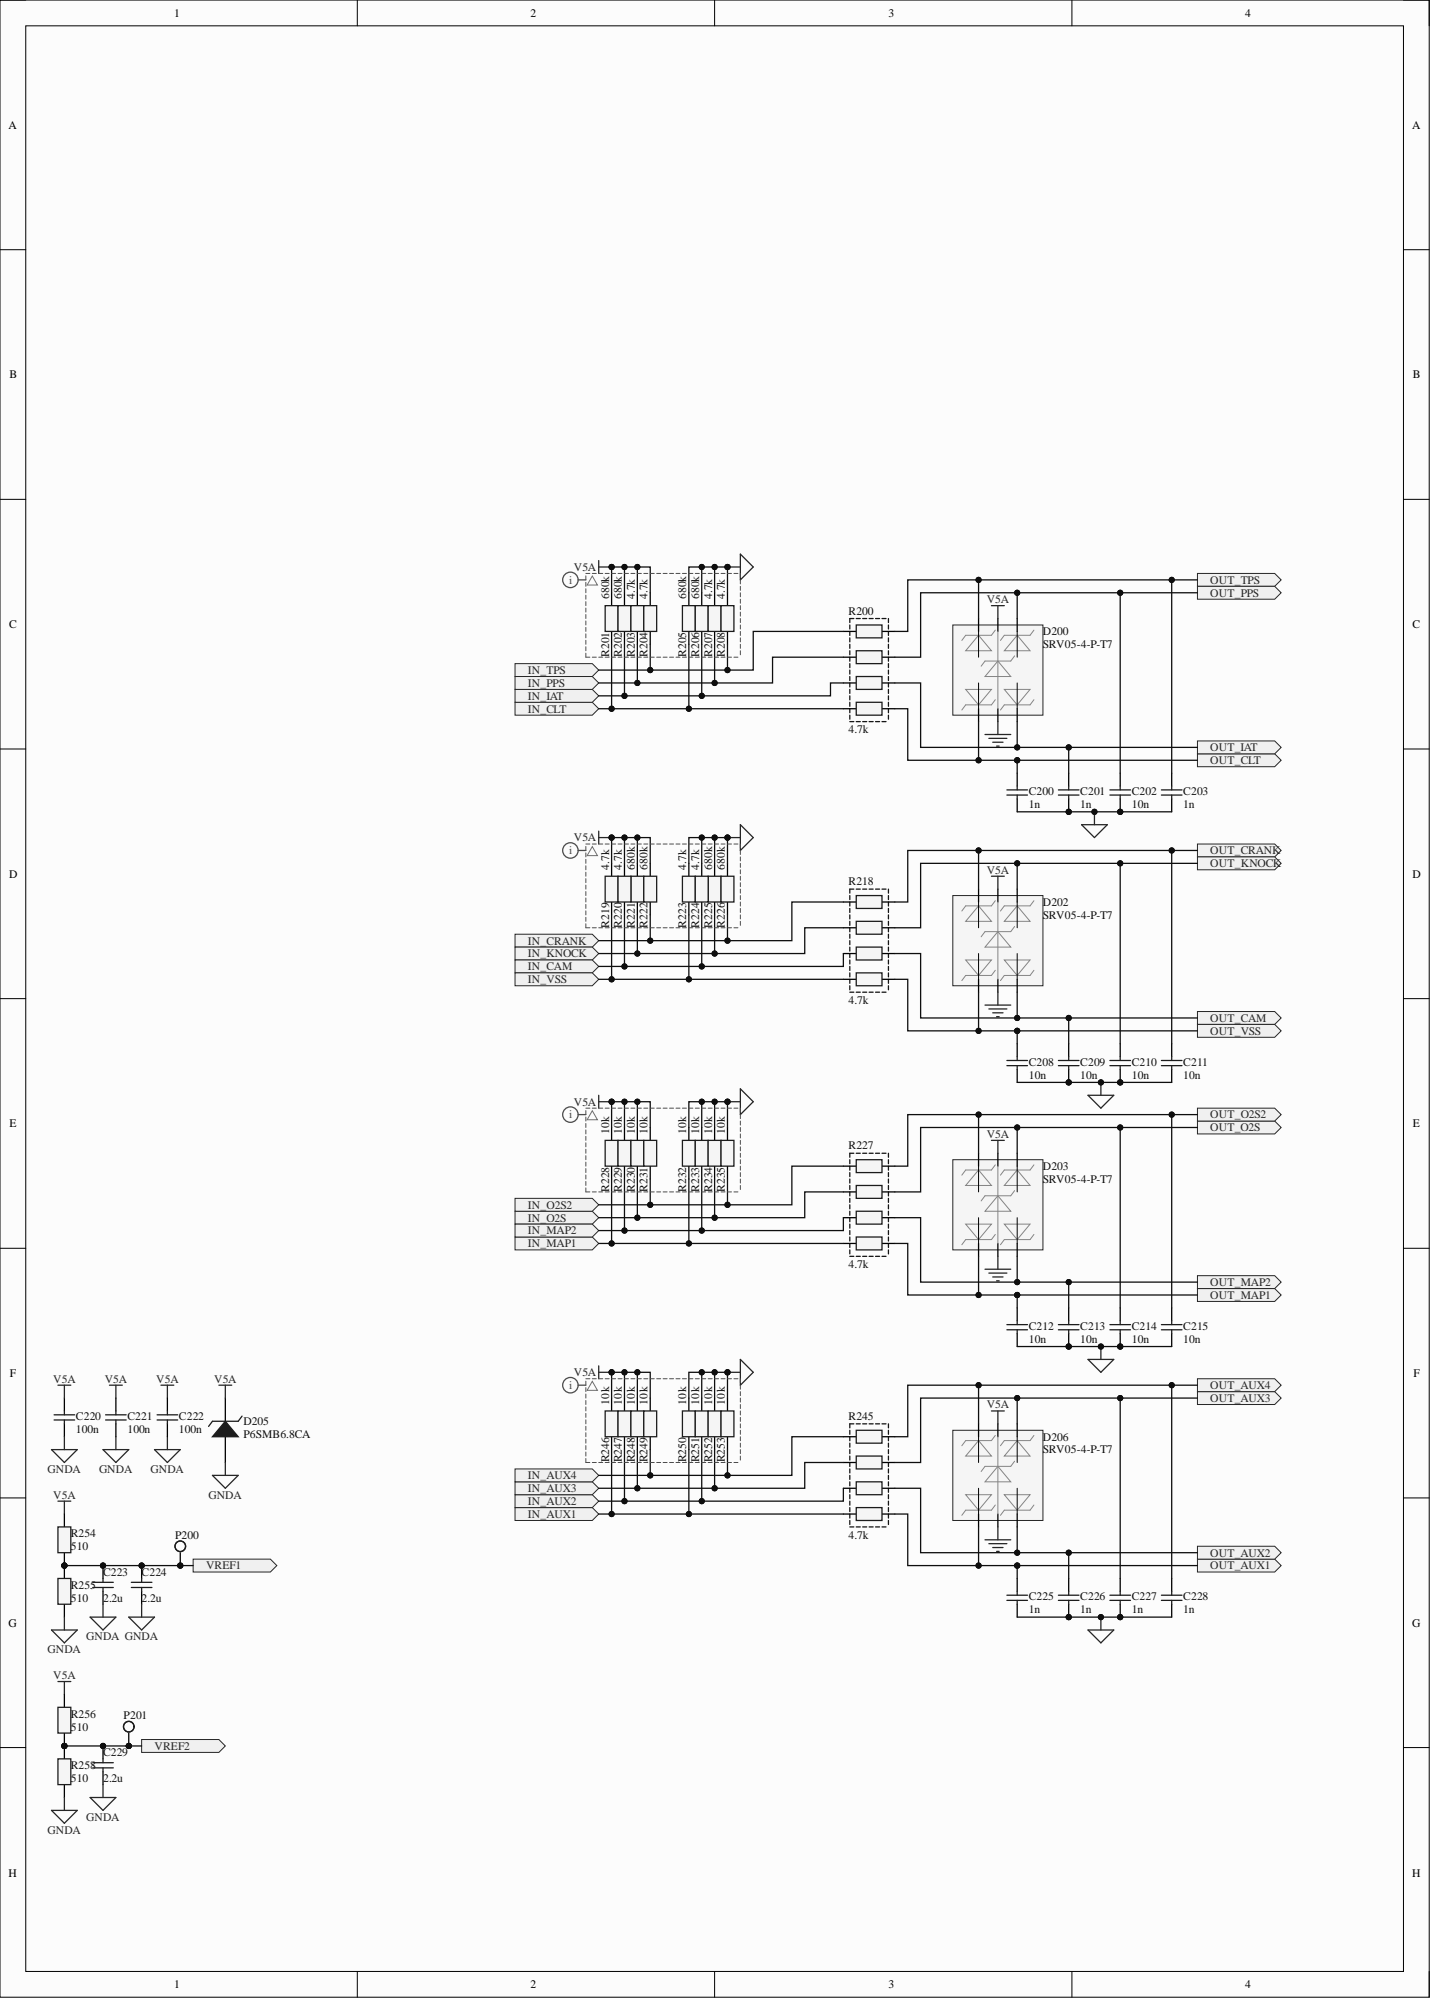
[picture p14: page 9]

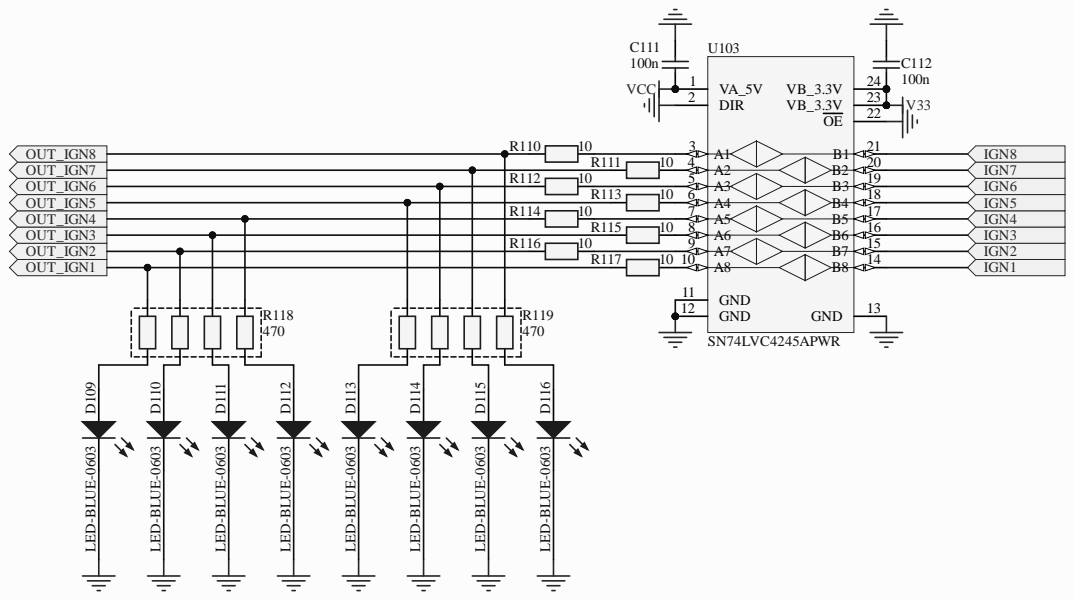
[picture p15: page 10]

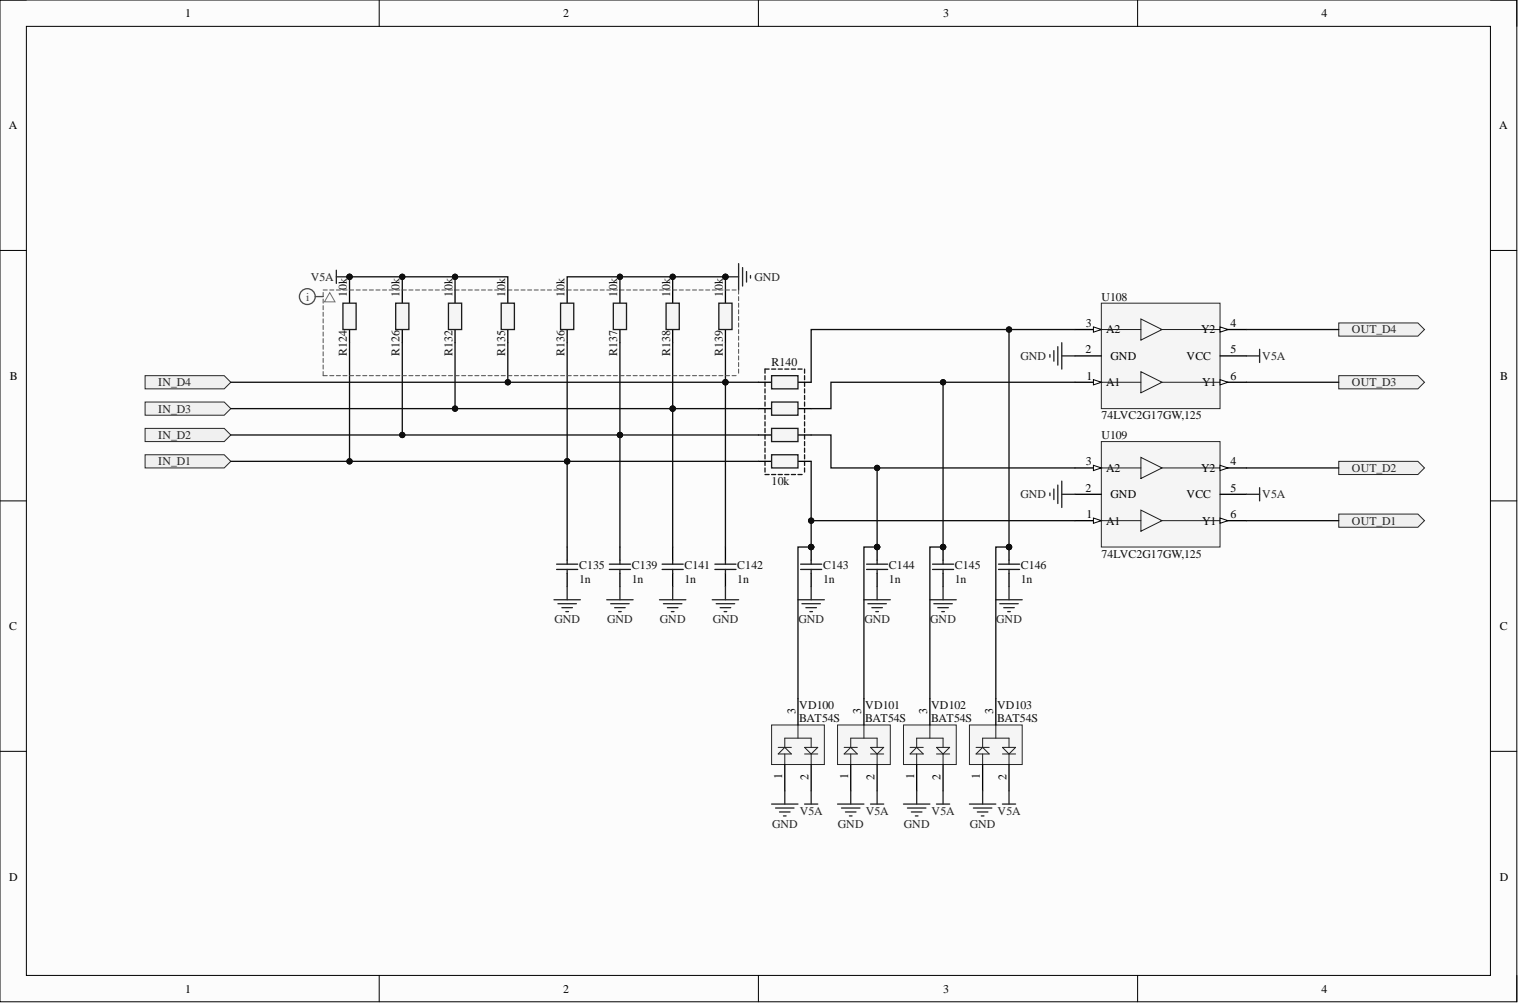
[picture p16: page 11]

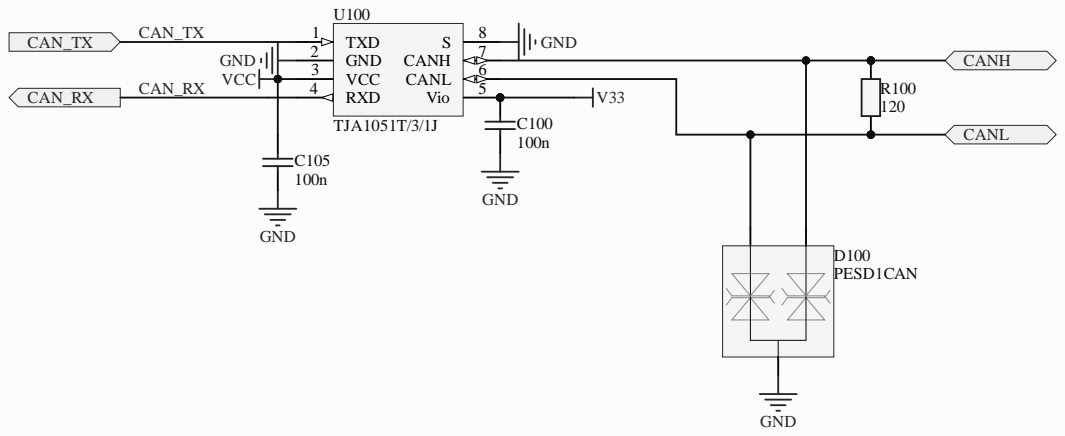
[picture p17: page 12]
D100 PESD1CAN; GND; TXD 1 GND 2 VCC 3; Vio; 5 RXD 4; CANL; 6 CANH; TJA1051T/3/1J; CAN_TX; CAN_RX; VCC; CANH; CANL C100 100n

VRE; _CRA; _CLT; IAT; _IAT; VIG; nRes; VBAT; SWCL; SPI2; _MIS; SPI3; I2C_SCL; SPI1; PWR_; GRE; u mcu.Sch; _IGN; 8.Sch; _can can.Sch; d.Sch; nRS; USB_; P USB_; USBI; A I2C_SCL UART8_RX UART8_TX UART2_RX UART2_TX; N VBAT; VCC; ACC_SC; ACC_; ACC_MIS; ACC_MO; BARO; sen; ors.Sc; LVC1; VBU; wer.Sch; USBID (PA; USBM (PA; USBP (PA; 8 SWDIO (PA13); N5 SWCLK (PA14); N6 nReset; _SCK (PC1; _MISO (PC1; _MOSI (PC1; I2C_SCL (PB1; 3 I2C_SDA (PB11); E4 UART2_TX (PD5); _SCK; _MISO (PB1; _MOSI (PB1; _PWM2 (PC6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

USBM USBP USBID VBUS

### COR2

Vdd 4; Vss 6; MCP6004; GNDA; IN1 (CRNK); OUT1; OUT2; OUT3; OUT4; C195 PIC19501 100n; PIC19502 COC2; PIR19502; PIR19501; PIR19601; PIR19602; PIR19603; PIR19604; PIR19605; PIR19606; PIR19607; PIR19608; COR3; PIR19701; PIR19702; PIR19703; PIR19705; PIR19704; PIR19706; PIR19707; PIR19708; COR4; PIU19501; PIU19502; PIU19503; PIU19504; PIU19505; PIU19506; PIU19507; PIU19508; PIU19509; PIU195010; PIU195011; PIU195012; PIU195013; PIU195014; COU1; PIC19501; POOUT1; POOUT2; POOUT3; POOUT4; POIN1 (CRNK)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

More accurate threshold for "raw" connection of VR sensors


RES 5; GND(1) 6; GND(2); 7 GND(3); 8 VDD; 9 VDD_IO; INT_2 11; INT_1 12; U106 LIS2DH12TR; VDD 10; INT DRDY; RES 3; Vdd IO 1; GND; LPS22HBTR; ACC_SCK ACC_CS ACC_MISO ACC_MOSI; BARO_SCL BARO_SDA

SCL/SPC 1
SDO/SA0 3
SDA/SDI/SDO 4

SCL/SPC 2
SDO/SA0 5


Hellen One : Power-Module interface

Reverse polarity and overvoltage protection
F410 V12_RAW

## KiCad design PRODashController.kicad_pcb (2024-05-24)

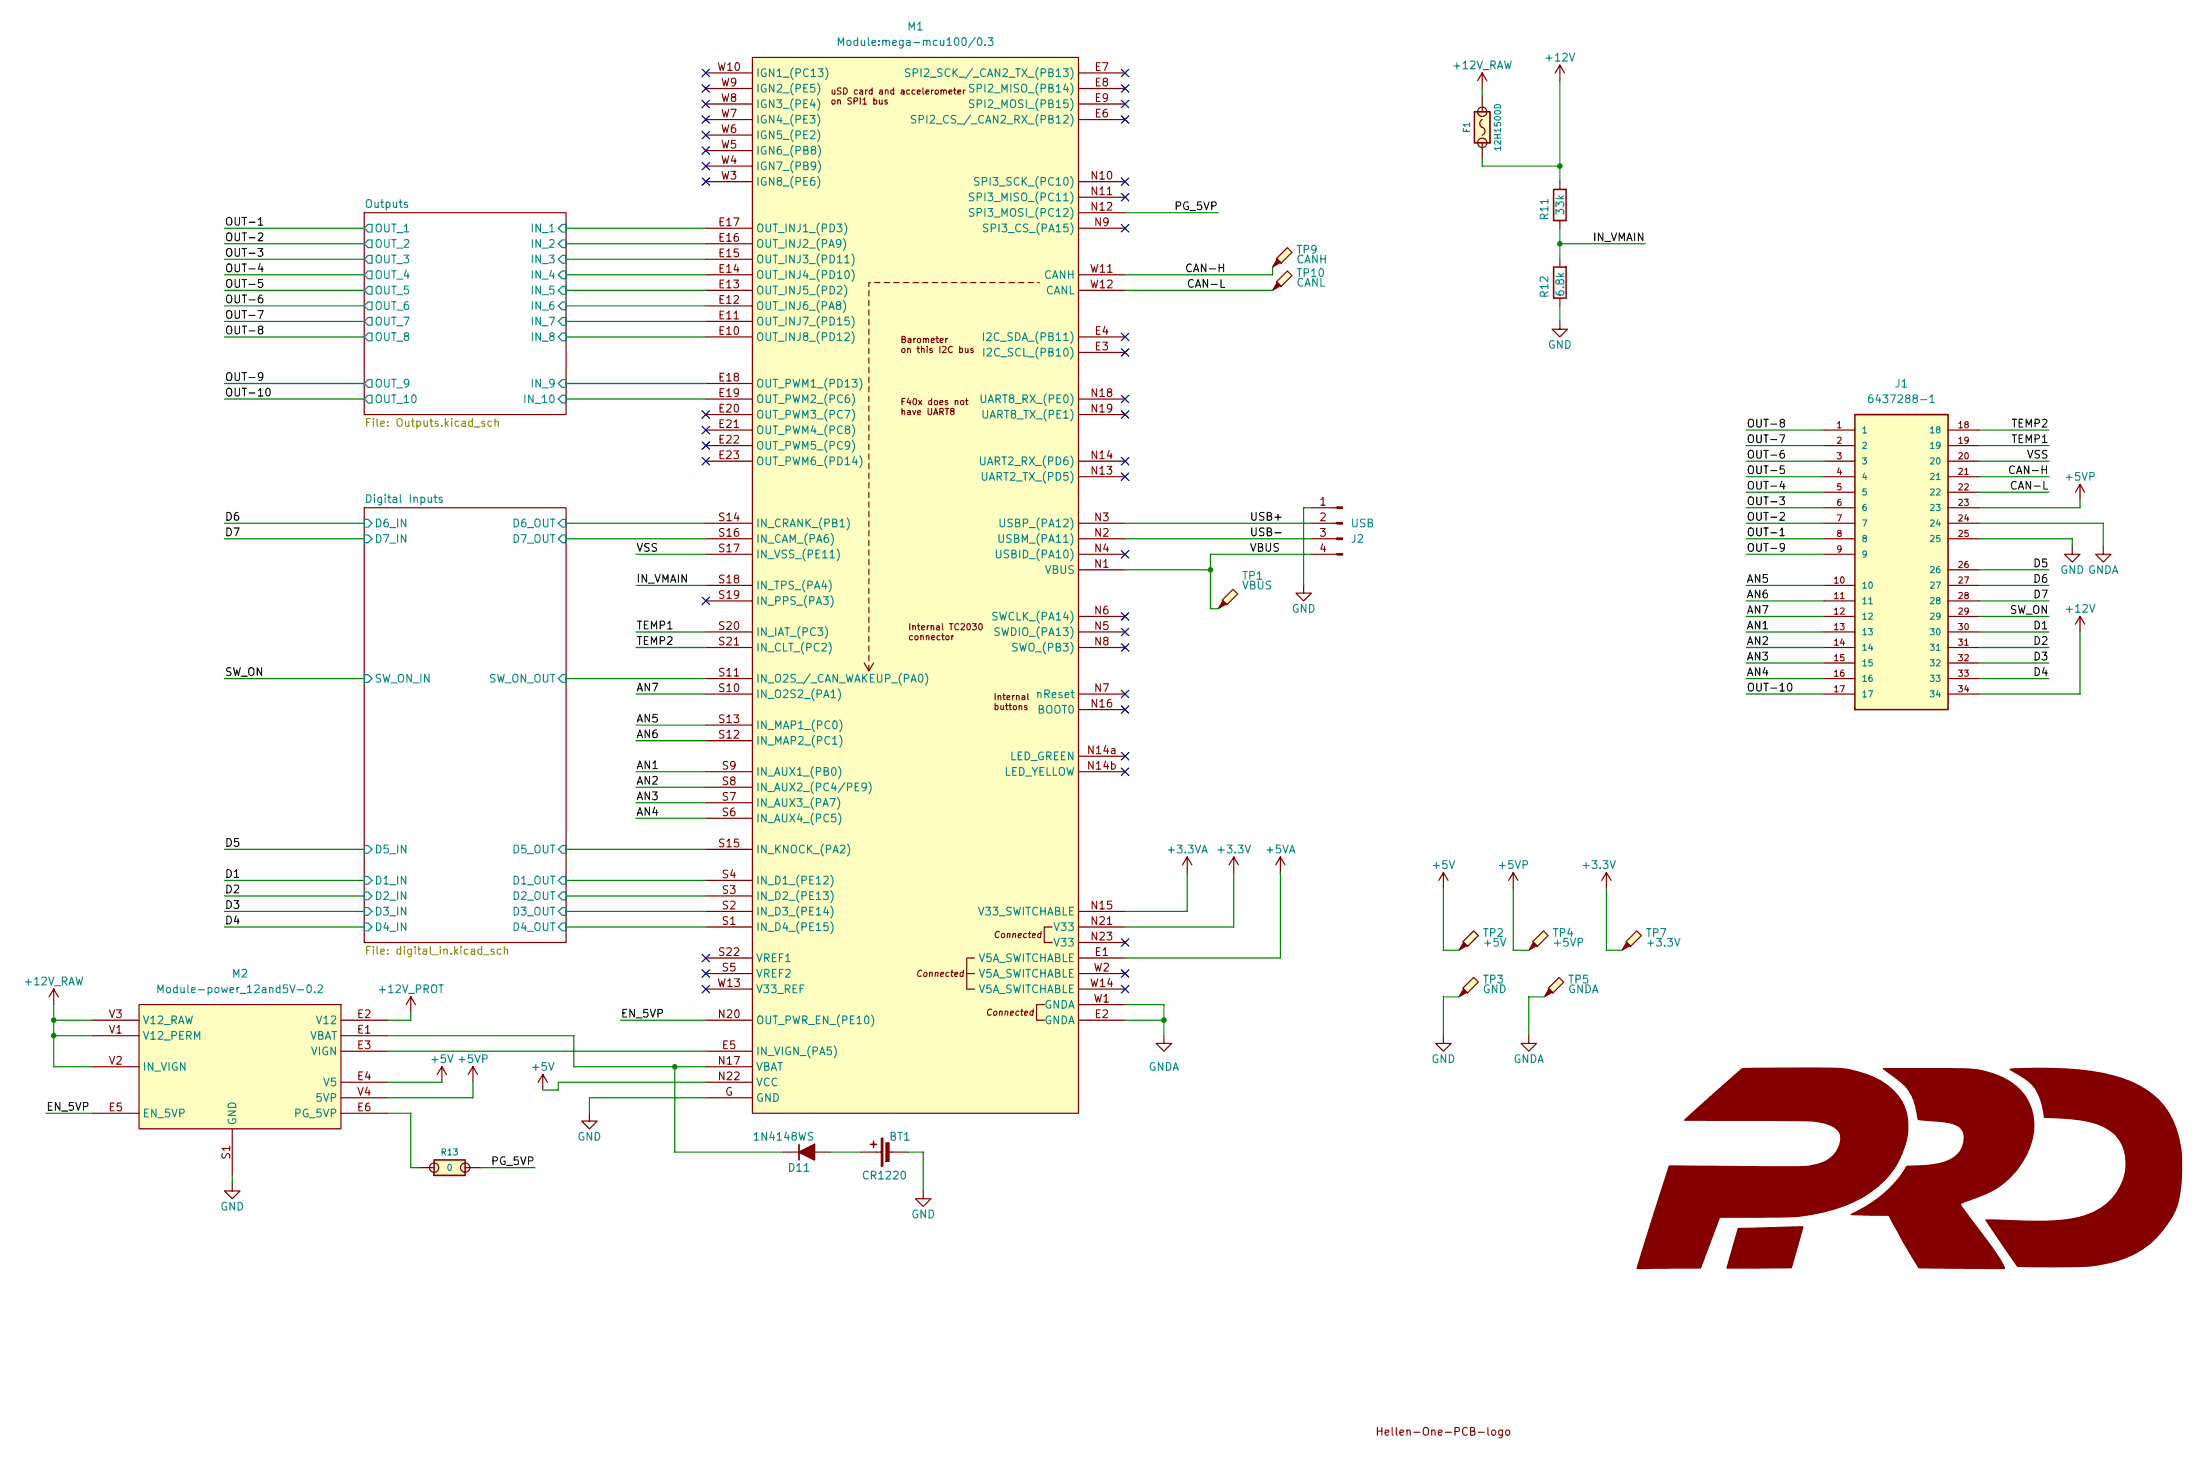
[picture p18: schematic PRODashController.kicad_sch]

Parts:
BT1: CR1220; CR1220-2; LCSC C70381
D11: 1N4148WS; SOD-323; LCSC C2128
F1: 12H1500D; PAD-1206-PAD; LCSC C182446
G1: LOGO
J1: 6437288-1; TE_6437288-1; PARTREV A1
J2: USB; JST_PH_B4B-PH-K_1x04_P2.00mm_Vertical; LCSC C5305780
M1: Module:mega-mcu100/0.3; mega-mcu100
M2: Module-power_12and5V-0.2; power_12and5V
R11: 33k; R0603; LCSC C4216
R12: 6.8k; R0603; LCSC C23212
R13: 0; R0805; LCSC C17477
TP1: VBUS; TestPoint_Pad_D1.0mm
TP2: +5V; TestPoint_Pad_D1.0mm
TP3: GND; TestPoint_Pad_D2.0mm
TP4: +5VP; TestPoint_Pad_D1.0mm
TP5: GNDA; TestPoint_Pad_D1.0mm
TP7: +3.3V; TestPoint_Pad_D1.0mm
TP9: CANH; TestPoint_Pad_D1.0mm
TP10: CANL; TestPoint_Pad_D1.0mm

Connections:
+3.3V: M1.N21 (V33), TP7.1
+3.3VA: M1.N15 (V33_SWITCHABLE)
+5V: M1.N22 (VCC), M2.E4 (V5), TP2.1
+5VA: M1.E1 (V5A_SWITCHABLE)
+5VP: J1.23, M2.V4 (5VP), TP4.1
+12V: F1.1, J1.34, R11.2
+12V_PROT: M2.E2 (V12); also elsewhere on the board
+12V_RAW: F1.2, M2.V1 (V12_PERM), M2.V2 (IN_VIGN), M2.V3 (V12_RAW); also elsewhere on the board
/AN1: J1.13, M1.S9 (IN_AUX1_(PB0))
/AN2: J1.14, M1.S8 (IN_AUX2_(PC4/PE9))
/AN3: J1.15, M1.S7 (IN_AUX3_(PA7))
/AN4: J1.16, M1.S6 (IN_AUX4_(PC5))
/AN5: J1.10, M1.S13 (IN_MAP1_(PC0))
/AN6: J1.11, M1.S12 (IN_MAP2_(PC1))
/AN7: J1.12, M1.S10 (IN_O2S2_(PA1))
/CAN-H: J1.21, M1.W11 (CANH), TP9.1
/CAN-L: J1.22, M1.W12 (CANL), TP10.1
/D1: J1.30; also elsewhere on the board
/D2: J1.31; also elsewhere on the board
/D3: J1.32; also elsewhere on the board
/D4: J1.33; also elsewhere on the board
/D5: J1.26; also elsewhere on the board
/D6: J1.27; also elsewhere on the board
/D7: J1.28; also elsewhere on the board
/Digital Inputs/D1_OUT: M1.S4 (IN_D1_(PE12)); also elsewhere on the board
/Digital Inputs/D2_OUT: M1.S3 (IN_D2_(PE13)); also elsewhere on the board
/Digital Inputs/D3_OUT: M1.S2 (IN_D3_(PE14)); also elsewhere on the board
/Digital Inputs/D4_OUT: M1.S1 (IN_D4_(PE15)); also elsewhere on the board
/Digital Inputs/D5_OUT: M1.S15 (IN_KNOCK_(PA2)); also elsewhere on the board
/Digital Inputs/D6_OUT: M1.S14 (IN_CRANK_(PB1)); also elsewhere on the board
/Digital Inputs/D7_OUT: M1.S16 (IN_CAM_(PA6)); also elsewhere on the board
/Digital Inputs/SW_ON_OUT: M1.S11 (IN_O2S_/_CAN_WAKEUP_(PA0)); also elsewhere on the board
/EN_5VP: M1.N20 (OUT_PWR_EN_(PE10)), M2.E5 (EN_5VP)
/IN_VMAIN: M1.S18 (IN_TPS_(PA4)), R11.1, R12.2
/OUT-1: J1.8; also elsewhere on the board
/OUT-2: J1.7; also elsewhere on the board
/OUT-3: J1.6; also elsewhere on the board
/OUT-4: J1.5; also elsewhere on the board
/OUT-5: J1.4; also elsewhere on the board
/OUT-6: J1.3; also elsewhere on the board
/OUT-7: J1.2; also elsewhere on the board
/OUT-8: J1.1; also elsewhere on the board
/OUT-9: J1.9; also elsewhere on the board
/OUT-10: J1.17; also elsewhere on the board
/Outputs/IN_1: M1.E17 (OUT_INJ1_(PD3)); also elsewhere on the board
/Outputs/IN_2: M1.E16 (OUT_INJ2_(PA9)); also elsewhere on the board
/Outputs/IN_3: M1.E15 (OUT_INJ3_(PD11)); also elsewhere on the board
/Outputs/IN_4: M1.E14 (OUT_INJ4_(PD10)); also elsewhere on the board
/Outputs/IN_5: M1.E13 (OUT_INJ5_(PD2)); also elsewhere on the board
/Outputs/IN_6: M1.E12 (OUT_INJ6_(PA8)); also elsewhere on the board
/Outputs/IN_7: M1.E11 (OUT_INJ7_(PD15)); also elsewhere on the board
/Outputs/IN_8: M1.E10 (OUT_INJ8_(PD12)); also elsewhere on the board
/Outputs/IN_9: M1.E18 (OUT_PWM1_(PD13)); also elsewhere on the board
/Outputs/IN_10: M1.E19 (OUT_PWM2_(PC6)); also elsewhere on the board
/PG_5VP: M1.N12 (SPI3_MOSI_(PC12)), R13.2
/SW_ON: J1.29; also elsewhere on the board
/TEMP1: J1.19, M1.S20 (IN_IAT_(PC3))
/TEMP2: J1.18, M1.S21 (IN_CLT_(PC2))
/USB+: J2.2, M1.N3 (USBP_(PA12))
/USB-: J2.3, M1.N2 (USBM_(PA11))
/VBUS: J2.4, M1.N1 (VBUS), TP1.1
/VSS: J1.20, M1.S17 (IN_VSS_(PE11))
GND: BT1.2 (-), J1.25, J2.1, M1.G (GND), M2.S1 (GND), R12.1, TP3.1; also elsewhere on the board
GNDA: J1.24, M1.E2 (GNDA), M1.W1 (GNDA), TP5.1
unnamed: BT1.1 (+), D11.2 (A)
unnamed: D11.1 (K), M1.N17 (VBAT), M2.E1 (VBAT)
unnamed: M1.E5 (IN_VIGN_(PA5)), M2.E3 (VIGN)
unnamed: M2.E6 (PG_5VP), R13.1

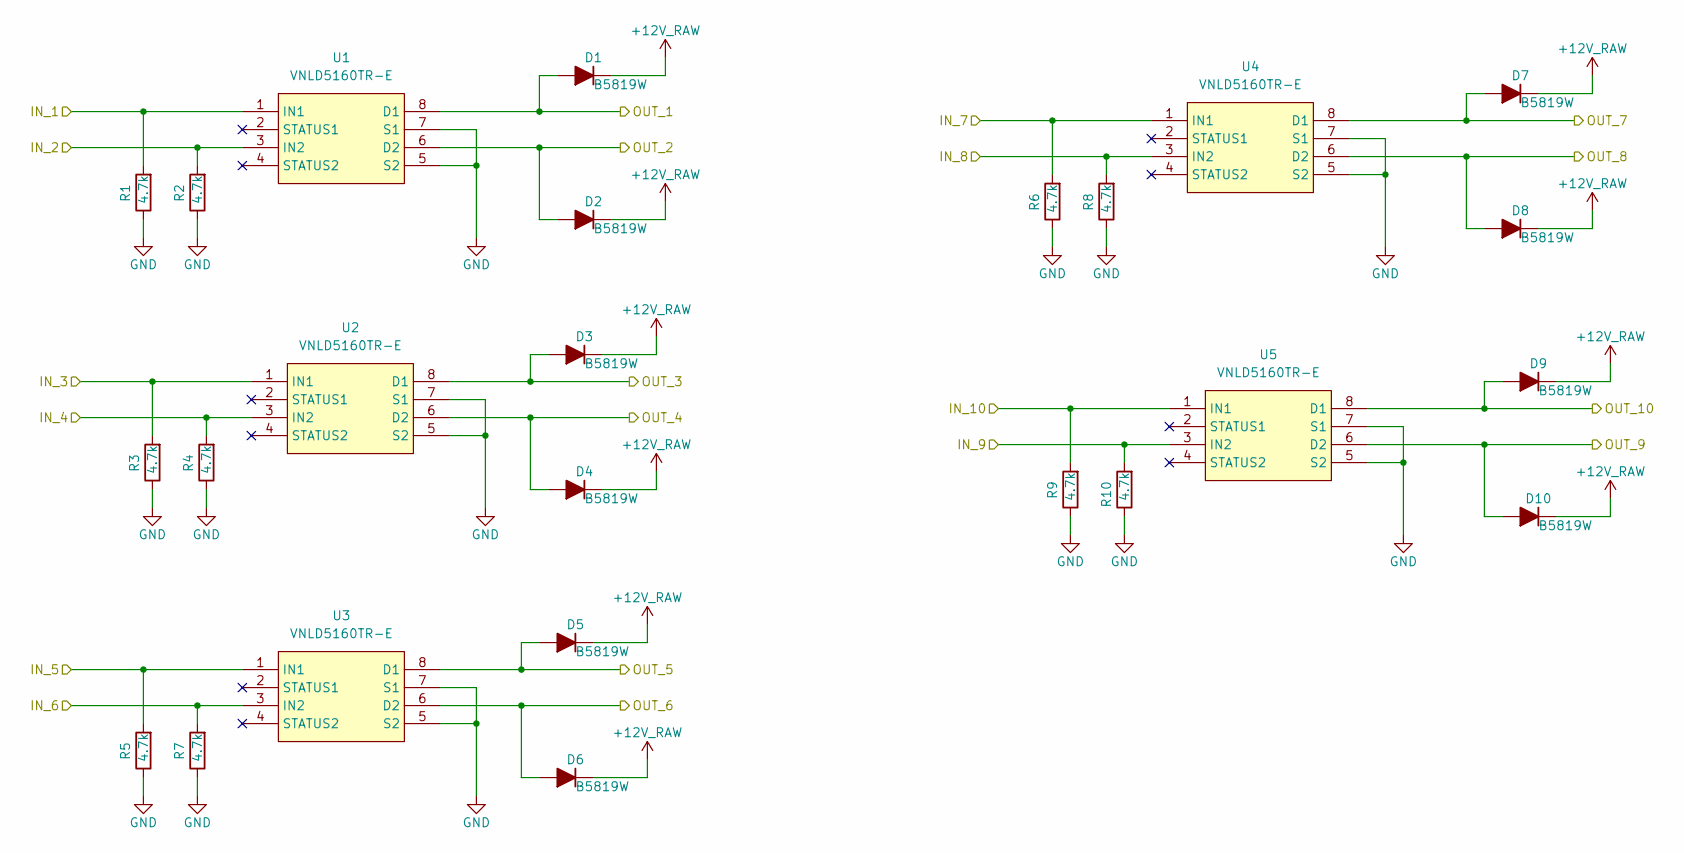
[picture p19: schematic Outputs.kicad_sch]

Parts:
D1, D2, D3, D4, D5, D6, D7, D8, D9, D10: B5819W; SOD-123; LCSC C8598
R1, R2, R3, R4, R5, R6, R7, R8, R9, R10: 4.7k; R0603; LCSC C23162
U1, U2, U3, U4, U5: VNLD5160TR-E; SOIC-8_3.9x4.9mm_P1.27mm; LCSC C377942

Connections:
+12V_RAW: D1.1 (K), D2.1 (K), D3.1 (K), D4.1 (K), D5.1 (K), D6.1 (K), D7.1 (K), D8.1 (K), D9.1 (K), D10.1 (K); also elsewhere on the board
/OUT-1: D1.2 (A), U1.8 (D1); also elsewhere on the board
/OUT-2: D2.2 (A), U1.6 (D2); also elsewhere on the board
/OUT-3: D3.2 (A), U2.8 (D1); also elsewhere on the board
/OUT-4: D4.2 (A), U2.6 (D2); also elsewhere on the board
/OUT-5: D5.2 (A), U3.8 (D1); also elsewhere on the board
/OUT-6: D6.2 (A), U3.6 (D2); also elsewhere on the board
/OUT-7: D7.2 (A), U4.8 (D1); also elsewhere on the board
/OUT-8: D8.2 (A), U4.6 (D2); also elsewhere on the board
/OUT-9: D10.2 (A), U5.6 (D2); also elsewhere on the board
/OUT-10: D9.2 (A), U5.8 (D1); also elsewhere on the board
/Outputs/IN_1: R1.2, U1.1 (IN1); also elsewhere on the board
/Outputs/IN_2: R2.2, U1.3 (IN2); also elsewhere on the board
/Outputs/IN_3: R3.2, U2.1 (IN1); also elsewhere on the board
/Outputs/IN_4: R4.2, U2.3 (IN2); also elsewhere on the board
/Outputs/IN_5: R5.2, U3.1 (IN1); also elsewhere on the board
/Outputs/IN_6: R7.2, U3.3 (IN2); also elsewhere on the board
/Outputs/IN_7: R6.2, U4.1 (IN1); also elsewhere on the board
/Outputs/IN_8: R8.2, U4.3 (IN2); also elsewhere on the board
/Outputs/IN_9: R10.2, U5.3 (IN2); also elsewhere on the board
/Outputs/IN_10: R9.2, U5.1 (IN1); also elsewhere on the board
GND: R1.1, R2.1, R3.1, R4.1, R5.1, R6.1, R7.1, R8.1, R9.1, R10.1, U1.5 (S2), U1.7 (S1), U2.5 (S2), U2.7 (S1), U3.5 (S2), U3.7 (S1), U4.5 (S2), U4.7 (S1), U5.5 (S2), U5.7 (S1); also elsewhere on the board

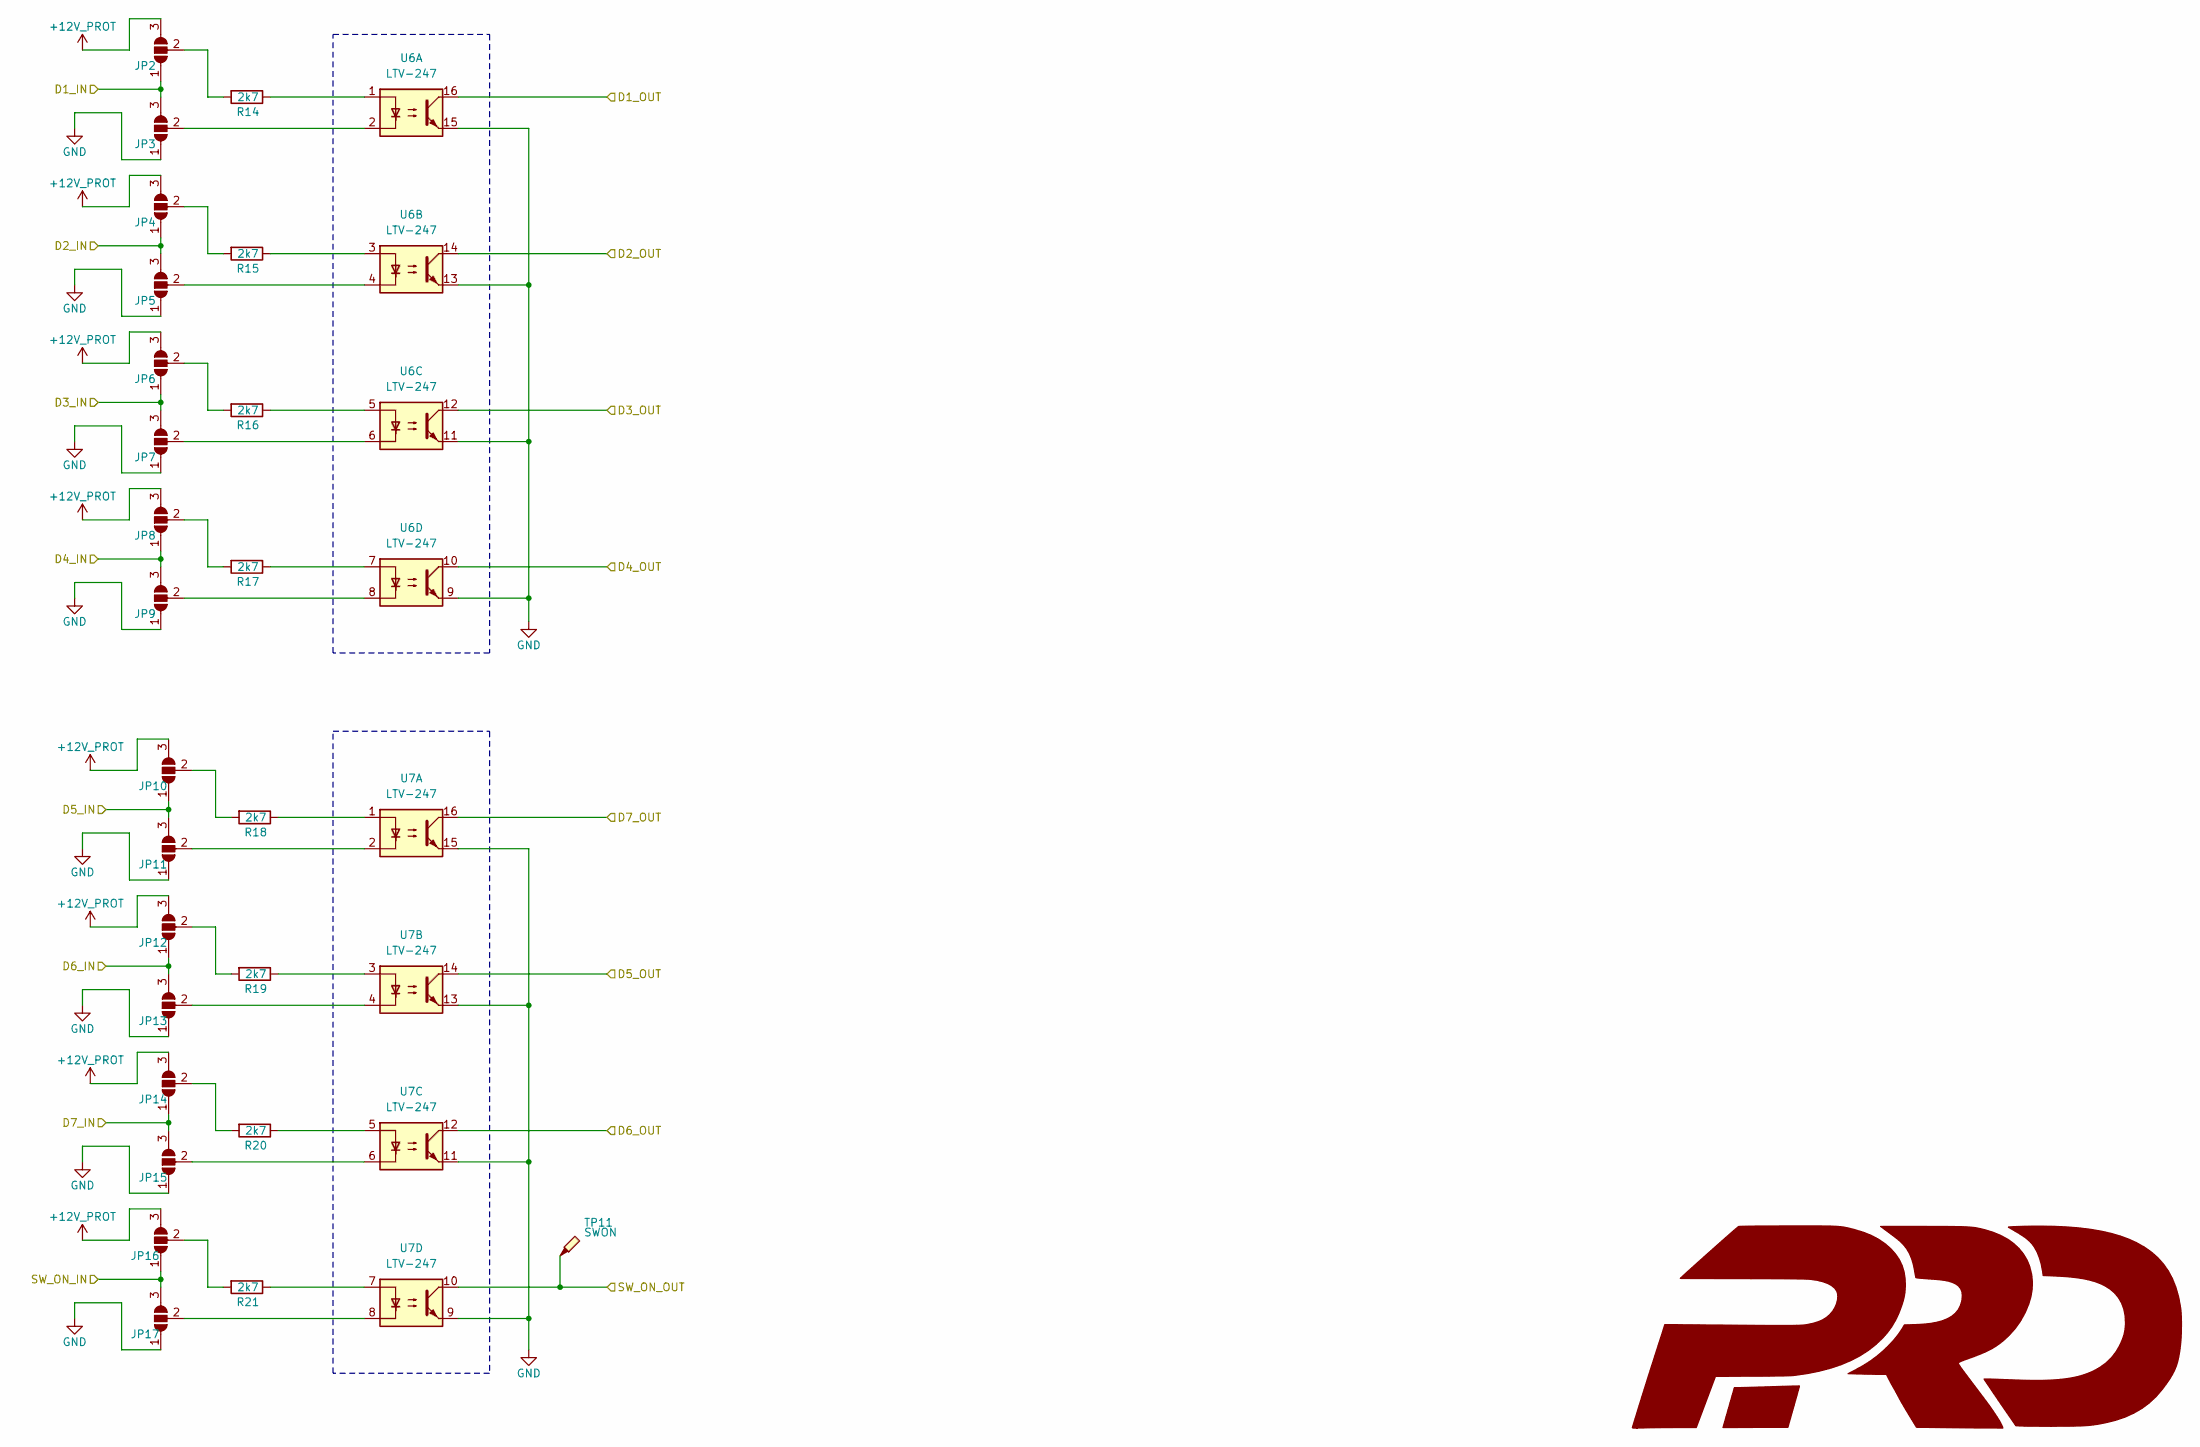
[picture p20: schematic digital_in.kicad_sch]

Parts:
JP2, JP3, JP4, JP5, JP6, JP7, JP8, JP9, JP10, JP11, JP12, JP13, JP14, JP15, JP16, JP17: SolderJumper_3_Open; SolderJumper-3_P1.3mm_Open_Pad1.0x1.5mm
R14, R15, R16, R17, R18, R19, R20, R21: 2k7; R0805; LCSC C17530
TP11: SWON; TestPoint_Pad_D1.0mm
U6, U7: LTV-247; SOP-16_4.4x10.4mm_P1.27mm; LCSC C115451

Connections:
+12V_PROT: JP2.3 (B), JP4.3 (B), JP6.3 (B), JP8.3 (B), JP10.3 (B), JP12.3 (B), JP14.3 (B), JP16.3 (B); also elsewhere on the board
/D1: JP2.1 (A), JP3.3 (B); also elsewhere on the board
/D2: JP4.1 (A), JP5.3 (B); also elsewhere on the board
/D3: JP6.1 (A), JP7.3 (B); also elsewhere on the board
/D4: JP8.1 (A), JP9.3 (B); also elsewhere on the board
/D5: JP10.1 (A), JP11.3 (B); also elsewhere on the board
/D6: JP12.1 (A), JP13.3 (B); also elsewhere on the board
/D7: JP14.1 (A), JP15.3 (B); also elsewhere on the board
/Digital Inputs/D1_OUT: U6.16; also elsewhere on the board
/Digital Inputs/D2_OUT: U6.14; also elsewhere on the board
/Digital Inputs/D3_OUT: U6.12; also elsewhere on the board
/Digital Inputs/D4_OUT: U6.10; also elsewhere on the board
/Digital Inputs/D5_OUT: U7.14; also elsewhere on the board
/Digital Inputs/D6_OUT: U7.12; also elsewhere on the board
/Digital Inputs/D7_OUT: U7.16; also elsewhere on the board
/Digital Inputs/SW_ON_OUT: TP11.1, U7.10; also elsewhere on the board
/SW_ON: JP16.1 (A), JP17.3 (B); also elsewhere on the board
GND: JP3.1 (A), JP5.1 (A), JP7.1 (A), JP9.1 (A), JP11.1 (A), JP13.1 (A), JP15.1 (A), JP17.1 (A), U6.9, U6.11, U6.13, U6.15, U7.9, U7.11, U7.13, U7.15; also elsewhere on the board
unnamed: JP2.2 (C), R14.2
unnamed: JP3.2 (C), U6.2
unnamed: JP4.2 (C), R15.2
unnamed: JP5.2 (C), U6.4
unnamed: JP6.2 (C), R16.2
unnamed: JP7.2 (C), U6.6
unnamed: JP8.2 (C), R17.2
unnamed: JP9.2 (C), U6.8
unnamed: JP10.2 (C), R18.2
unnamed: JP11.2 (C), U7.2
unnamed: JP12.2 (C), R19.2
unnamed: JP13.2 (C), U7.4
unnamed: JP14.2 (C), R20.2
unnamed: JP15.2 (C), U7.6
unnamed: JP16.2 (C), R21.2
unnamed: JP17.2 (C), U7.8
unnamed: R14.1, U6.1
unnamed: R15.1, U6.3
unnamed: R16.1, U6.5
unnamed: R17.1, U6.7
unnamed: R18.1, U7.1
unnamed: R19.1, U7.3
unnamed: R20.1, U7.5
unnamed: R21.1, U7.7

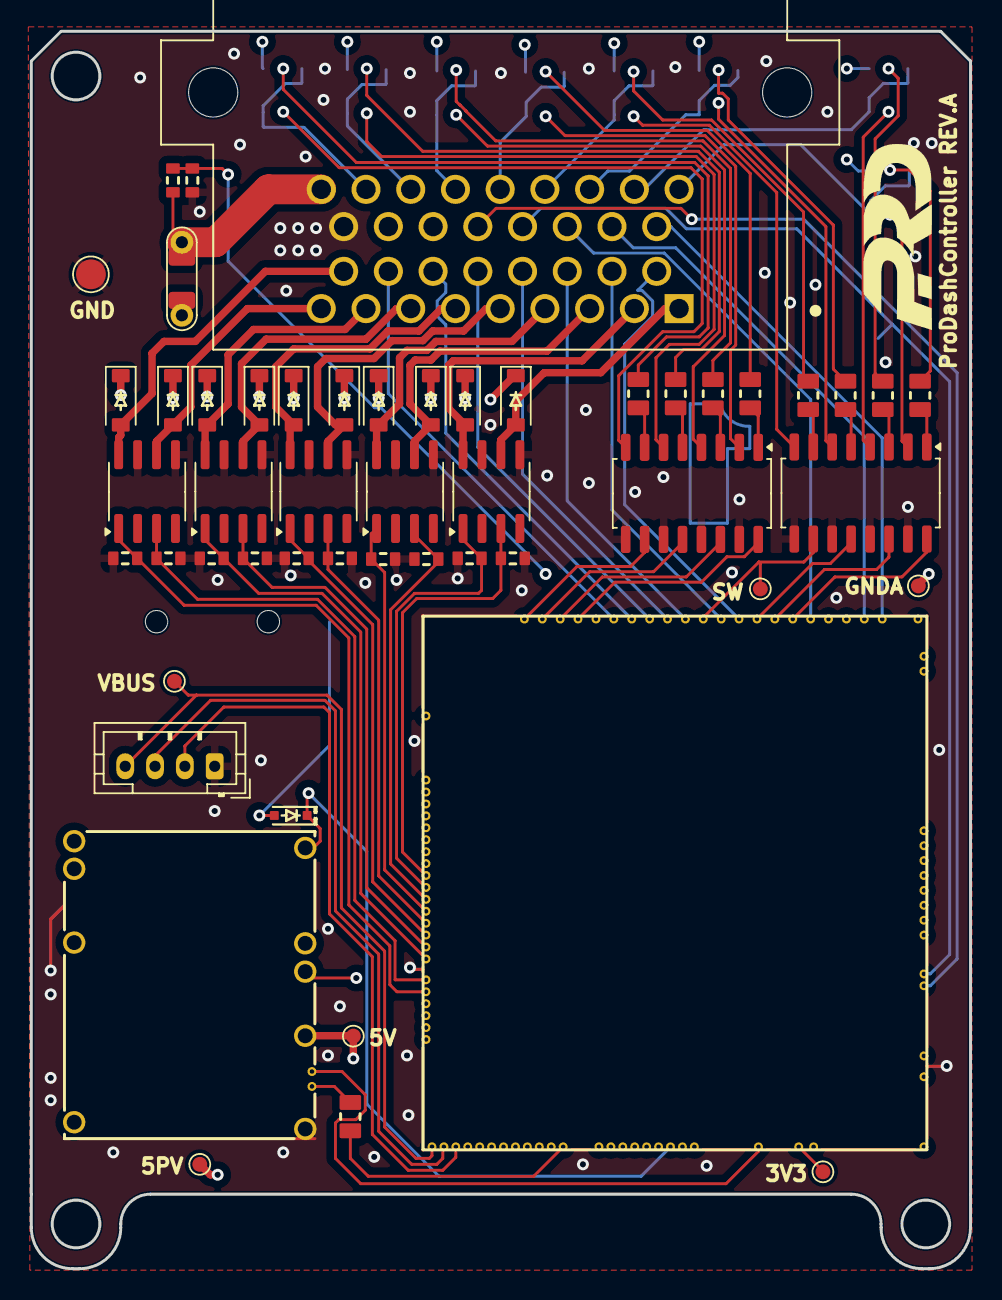
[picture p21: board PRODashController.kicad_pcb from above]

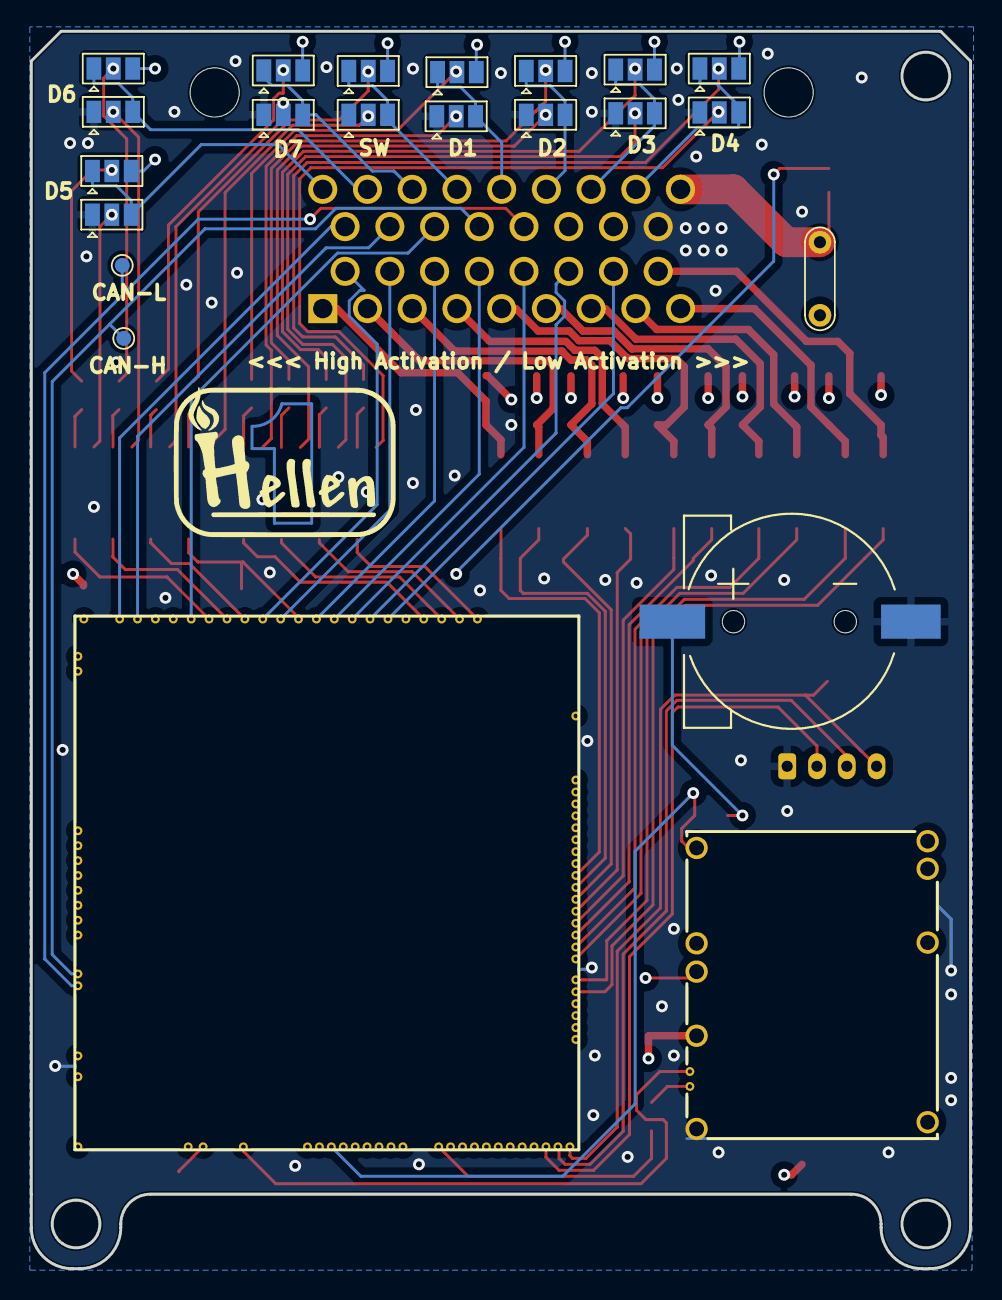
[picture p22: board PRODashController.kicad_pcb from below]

Board: 4 copper layers, 63.0 x 83.0 mm, 72 parts (20 on the bottom side), 90 nets.

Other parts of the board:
G2: LOGO; PRO_LOGO

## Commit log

2024-05-24 Rev A
    [Outputs.kicad_sch, PCBoutline.dxf, PRODashController.kicad_pcb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]
2024-05-24 [skip actions] Auto-generated board v2.1
    [PRODashController-B_Cu.gbl, PRODashController-B_Mask.gbs, PRODashController-B_Paste.gbp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]
2024-06-02 GHA says update kicad6-libraries
2024-07-19 Rev A - New Bom-Remplase
    [bom_replace_PRODashController-A.csv]
2024-07-19 Rev A - Pull-Up/Downs
    [bom_replace_PRODashController-A.csv]
2024-07-19 Rev A - Fix Typo
    [bom_replace_PRODashController-A.csv]
